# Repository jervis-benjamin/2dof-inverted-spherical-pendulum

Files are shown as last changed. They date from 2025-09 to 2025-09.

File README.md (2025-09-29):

# 2dof Inverted Spherical Pendulum

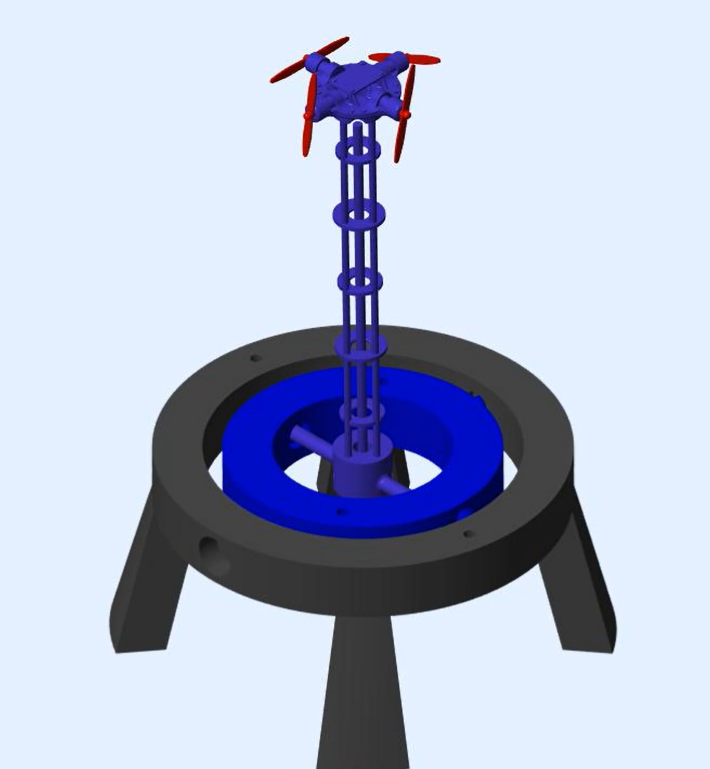
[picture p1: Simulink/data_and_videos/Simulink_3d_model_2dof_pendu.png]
model of the pendulum in Simulink


## Overview 🚀🌌
This project aims to keep an inverted pendulum (free to rotate about 2 axis) upright and balanced using orthogonally placed motors and propellors. Features include dedicated PID controllers, an extended Kalman filter for IMU sensor fusion, modeling system dynamics through Simulink, and hardware implementation through ESP32/Arduino components and CAD + 3D printing.

The goal of this project was to learn fundamentals of controls and design. Many of the components in this project are far from perfect, but they represent the time I’ve spent exploring a topic I care about.

### Here is the project broken up into its major sections, explained in further detail below:
- *CAD/Structure Design* 🧮📐
- *Simulation and Modeling* 🎯📊
- *Electronics, Controller Software, and Implementation* 🛠️🔌

### If you are interested in replicating or improving this project, here are the tools used:
*(These are just what I used, there are always better and more accessible options)*
- **CAD** -> Solidworks
- **3D printing** -> Cura, Ender 3
- **Simulation** -> Simulink
- **Controller Software** -> C++ (using an Arduino framework on Platform.io via VS Code)
- **Telemetry** -> VS Code Teleplot Extension

### Notable Materials/Items Used:
- ESP32 Dev Board
- Adafruit MPU-6050 6-DoF Accel and Gyro Sensor
- L298N DC Motor Driver Module (x2)
- LM2596 DC-DC Buck Power Converter Module
- 7x16 drone DC motors and propellers (x4)
- 18650 batteries (x2)
- 608 2RS Ball Bearings (x4)
- PLA filament rolls

## CAD/Structure Design 🧮📐
As mentioned before, all structural parts were custom made, 3D modeled and printed from PLA. This was to support the iterative process of building and testing prototypes, as well as enabling me to grow more on my knowledge of CAD and 3D printing. 

**The general structure can be mainly broken down into two sections:**
- The pendulum and supporting components
  - This includes the pendulum head (which houses the IMU and 4 motors), and the rod section (which extends the pendulum head down to the gimbal points).
- The bed
  - This includes the gimbal pieces which provide the 2 degrees of freedom, the stand which contains the pendulum, and the “electronics bay” which houses components such as the ESP32, battery, and motor control boards.
 
Within the CAD directory are both the .stl files and well as the Solidworks part + assembly files that were used to create this project.

## Simulation and Modeling 🎯📊
Euler-Langrage Equations of motion (overview of derivation linked in this pdf):

*Euler-Langrage Equations of motion for the pendulum*

To model the pendulum’s dynamics and simulate the control logic used, I learned how to use Simulink. There are many things to refine as this is the first model I have made in Simulink, but below is the general functionalities and structure of the program:

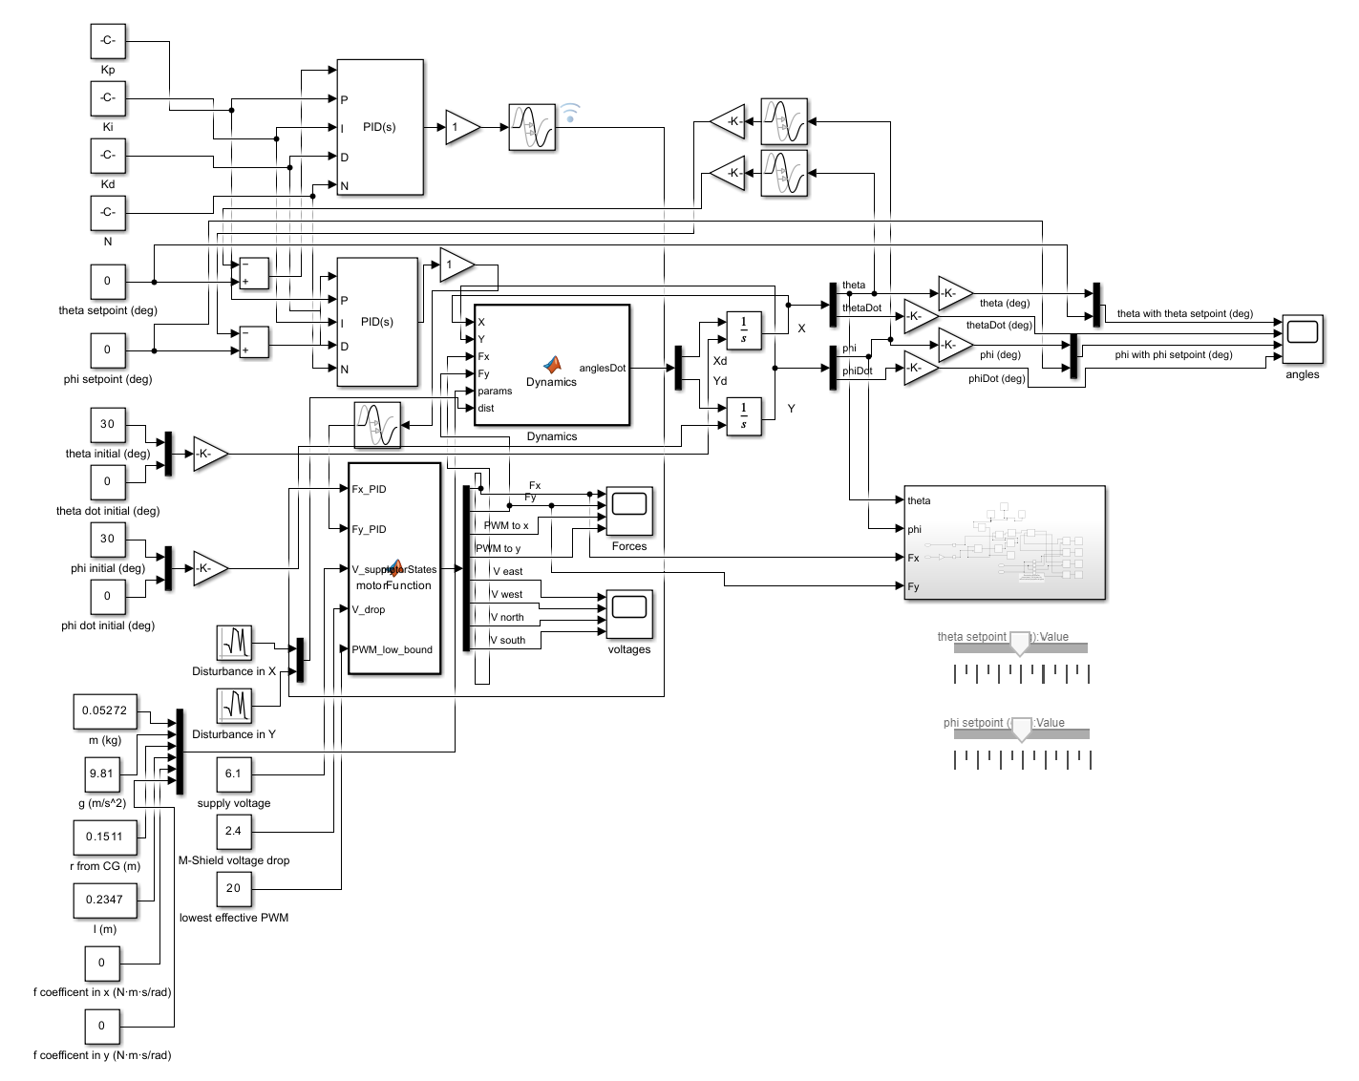
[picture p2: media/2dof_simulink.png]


- Implements PID control loops for each axis of control.
- Models dynamics via Euler-Lagrange equations of state as MATLAB functions.
- Mimics motor algorithms in controller code to show how a PID control output is being converted to a motor signal.
- Takes in parameters of real hardware
- Has the option to control the setpoint in real time to control the pendulum on user inputs.

**Simulation outputs**
- 3D visualization of pendulum performance (found in: Simulink/data_and_videos)
- Plots of relevant data such as angles, setpoints, forces, and motor commands over time
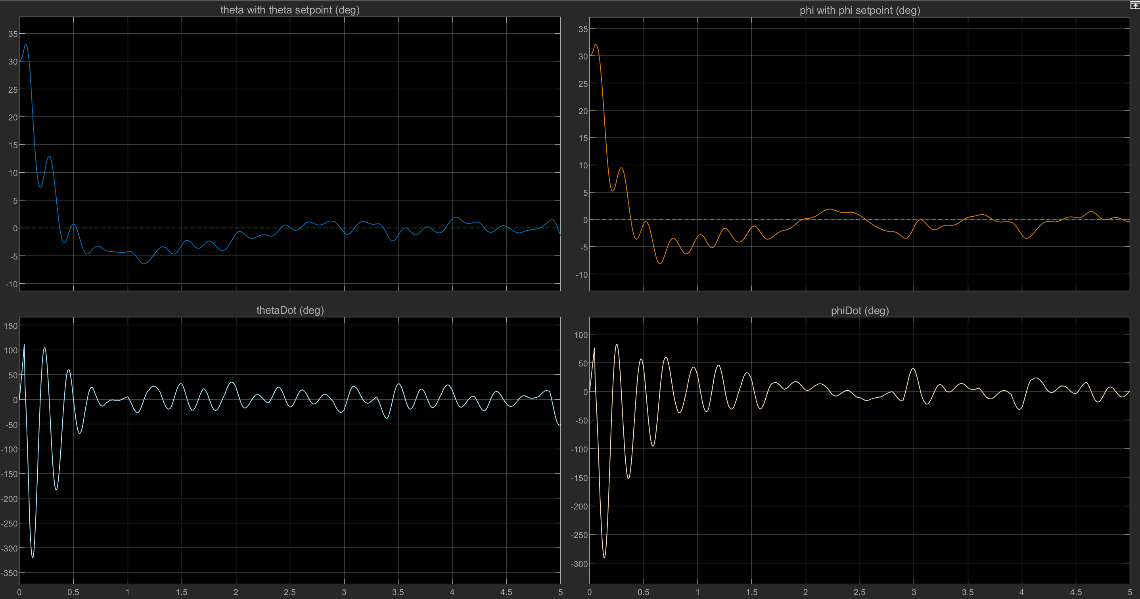
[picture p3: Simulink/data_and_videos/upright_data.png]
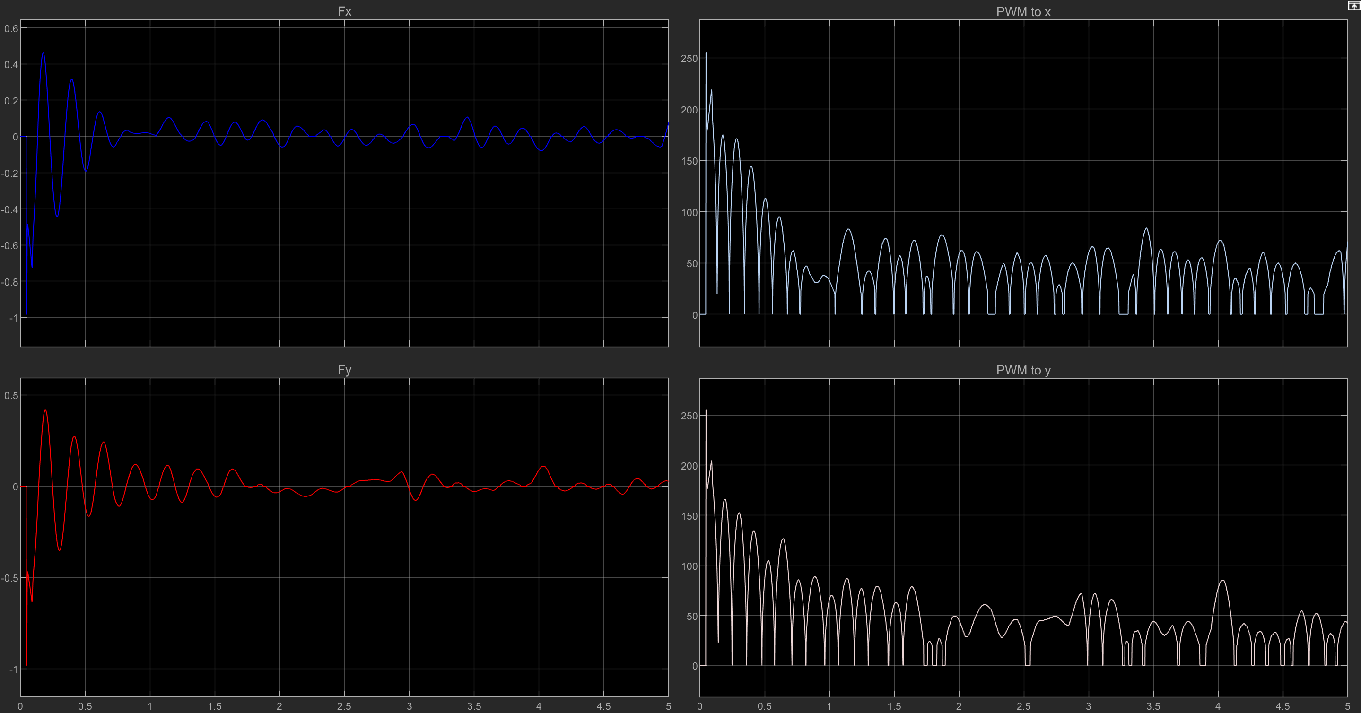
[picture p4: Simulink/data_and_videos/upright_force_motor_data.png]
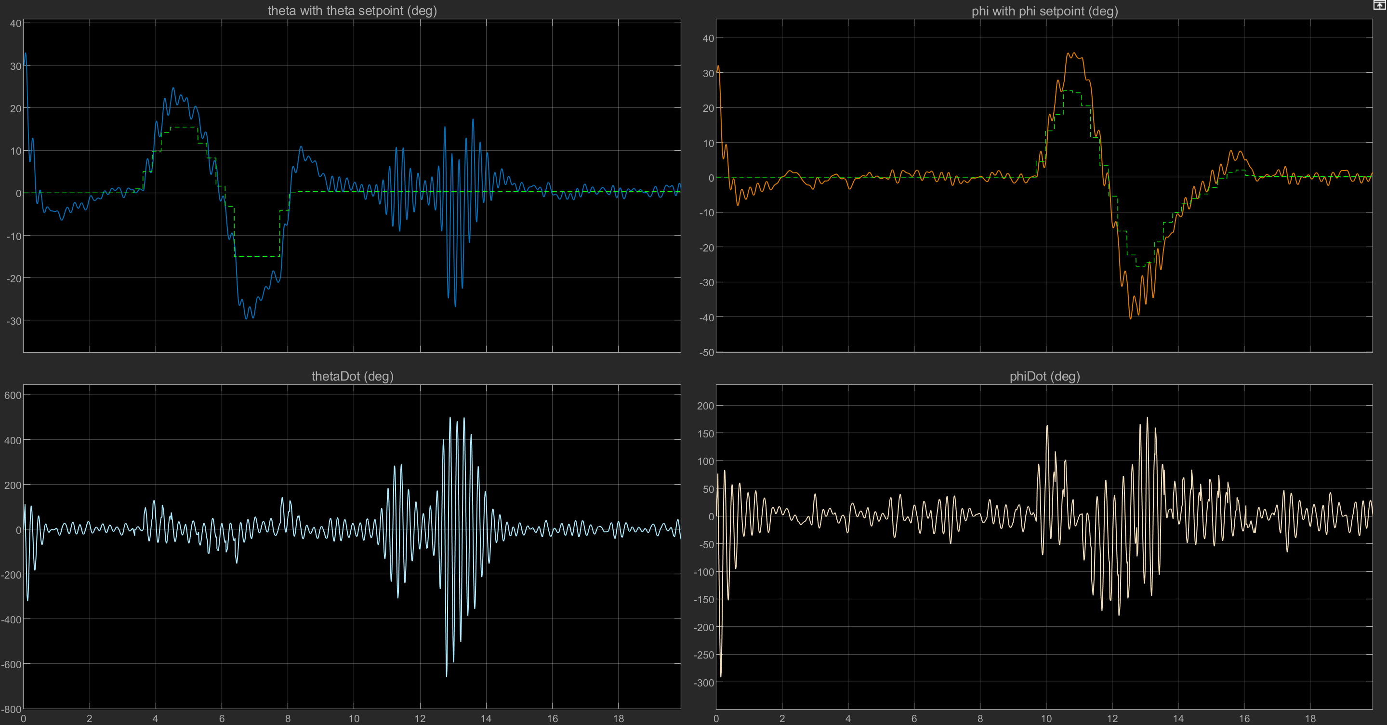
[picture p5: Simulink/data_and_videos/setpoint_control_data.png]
   

## Electronics, Controller Software, and Implementation 🛠️🔌
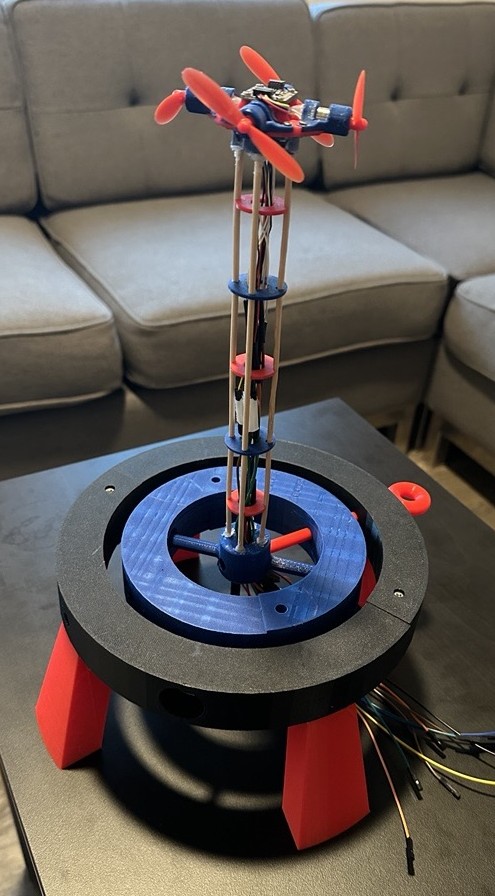
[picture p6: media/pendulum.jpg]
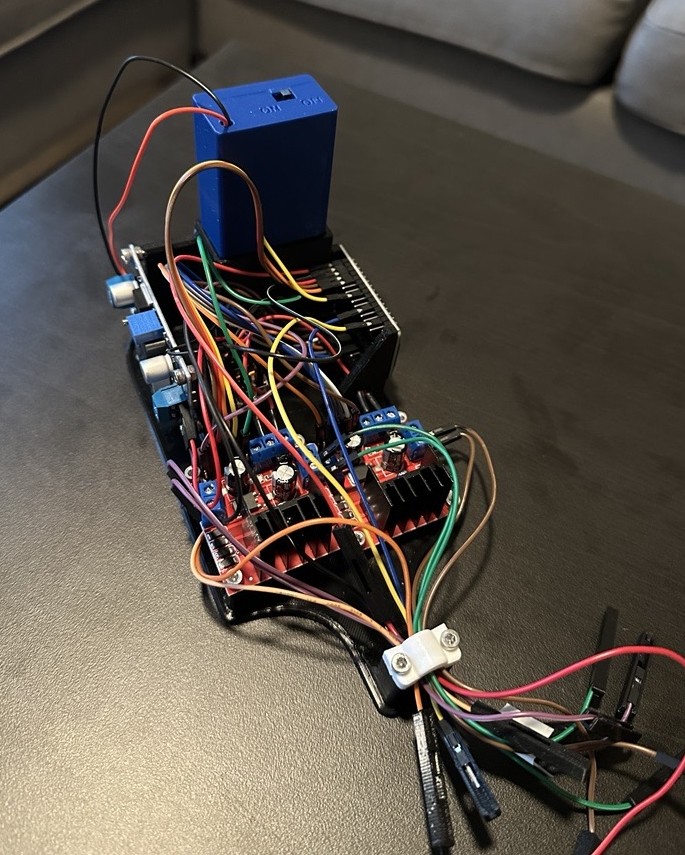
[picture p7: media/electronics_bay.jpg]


To interface with the hardware, I utilized a C++ controller program which ran on an ESP32 that linked communication between the IMU and motors. The step is the culmination of the CAD and design work to create a physical model.

**Features:**
- To gather usable angular position data from the IMU, an extended Kalman filter was utilized for accelerometer and gyroscope sensor fusion.
- Using the VS Code Teleplot extension, the controller code could display IMU and motor data as moving plots.
- The controller code supported user interaction via serial commands, allowing the user to change the pendulum setpoint at any time or run preprogrammed setpoint control programs.

Through testing and tunning, the pendulum was able to balance, though only within a small range. After referencing the simulation model, controller code, and the hardware performance, the biggest limitation to stability was the time taken for the propellors to spin fast enough to produce the required thrust. While the pendulum’s performance was not robust as originally planned, further steps can be taken for the future of this project (which are explained in the section below)

## Future Steps🛰️🔭
Overall, the large delay in the time that the propellors spin fast enough to provide the required torque prevents the level of stability that I am aiming for. Without much support, the pendulum fails to keep upright within a range larger than 5 degrees. In the future, I am planning to either account for this by implementing faster hardware or allowing the controller to better anticipate these delays. 

Additionally, I am hoping to increase the complexity of this project to allow me to dive deeper and apply more relevant concepts within controls. For example, I am considering adding another degree of freedom (rotation about the z axis), as well as integrating more complex controller logic such as LQR. Moreover, to better reflect the applicability of this project, I think it may be interesting to switch propulsion to cold gas thrusters to reflect a spacecraft's ability to use an RCS for attitude control.

To conclude, though the current set up is unable to bring the level of stability I was aiming for, I learned a lot through this process from software design to hardware implementation. I am determined to learn even more, and work on the ideas mentioned above to create a more sophisticated controls project.

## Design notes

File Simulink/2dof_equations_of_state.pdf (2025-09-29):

# 2dof Equations of State, Basic Overview

## References:

θ = tilt about the y axis, | ϕ = tilt about the x axis
rcm = length to the center of mass, | l = length of pendulum

L = T − U = KE − P E

d

dt
∂L
∂q˙
−

∂L
∂q = Q

Kinematics:

x = rcm sin θ cos ϕ, | y = rcm sin θ, | z = rcm cos θ cos ϕ

x˙ = rcm

˙θ cos θ cos ϕ − rcmϕ˙ sin θ sin ϕ

y˙ = rcmϕ˙ cos ϕ

z˙ = −rcm

˙θ sin θ cos ϕ − rcmϕ˙ cos θ sin ϕ

T =

1

2mv² =
1

2m( ˙x + ˙y + ˙z) = 1

2mr²

cm(ϕ˙² + ˙θ
2

cos² ϕ)

U = mgz = mgrcm cos θ cos ϕ

## Lagrangian

L = T − U =

1
2

mr²

cmϕ˙² +

1
2

mr²
cm

˙θ
2

cos² ϕ − mgrcm cos θ cos ϕ

—

1

## Equations of Motion

d

dt
∂L
∂ ˙θ
−

∂L
∂θ = τθ

d

dt
∂L
∂ϕ˙
−

∂L
∂ϕ = τϕ

Thus:

mr²
cm

¨θ cos² ϕ − mr²
cm

˙θϕ˙ sin(2ϕ) − mgrcm sin θ cos ϕ = τθ = Fxl

mrcmϕ¨ +

1
2

mr²
cm

˙θ
2
sin(2ϕ) − mgrcm cos θ sin ϕ = τϕ = Fyl

—

## State-Space Equations

Define states:
x1 = θ, | x2 = ˙θ, | y1 = ϕ, | y2 = ϕ˙

Dynamics:
x˙ 1 = x2 = ˙θ
x˙ 2 = ¨θ = | Fxl
mrcm cos² ϕ
| + | ˙θϕ˙ sin(2ϕ)
| | cos² ϕ | + g sin θ rcm cos ϕ

y˙1 = y2 = ϕ˙

y˙2 = ϕ¨ = | Fxl
mr²
| cm − ˙θ
| 2 | sin(2ϕ)
| | 2 + | g cos θ sin ϕ rcm

2

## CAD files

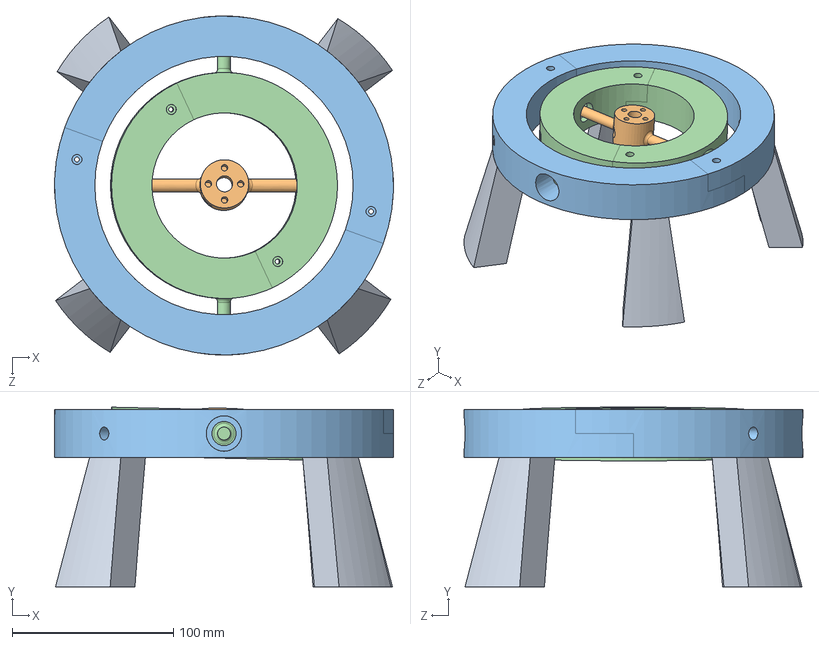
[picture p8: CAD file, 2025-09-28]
cad/solidworks/assemblies/2dof Bed.SLDASM
210.0 x 111.3 x 210.0 mm
inner_ring_2dof x 2
outer_ring_2dof x 2
core_2dof
leg_2dof x 4

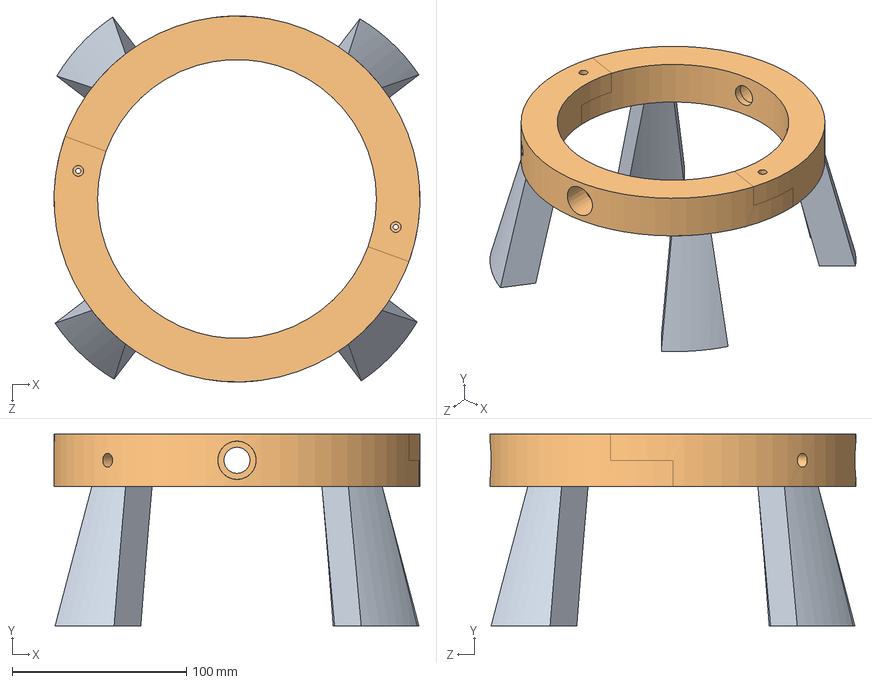
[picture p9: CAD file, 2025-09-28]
cad/solidworks/assemblies/Outer Ring Assembly.SLDASM
210.0 x 110.0 x 210.0 mm
outer_ring_2dof x 2
leg_2dof x 4

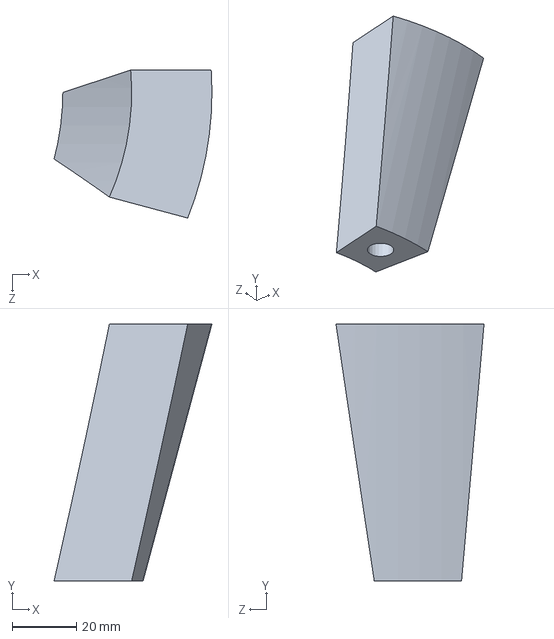
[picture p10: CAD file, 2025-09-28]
cad/solidworks/bed/leg_2dof.SLDPRT
49.2 x 80.0 x 46.1 mm

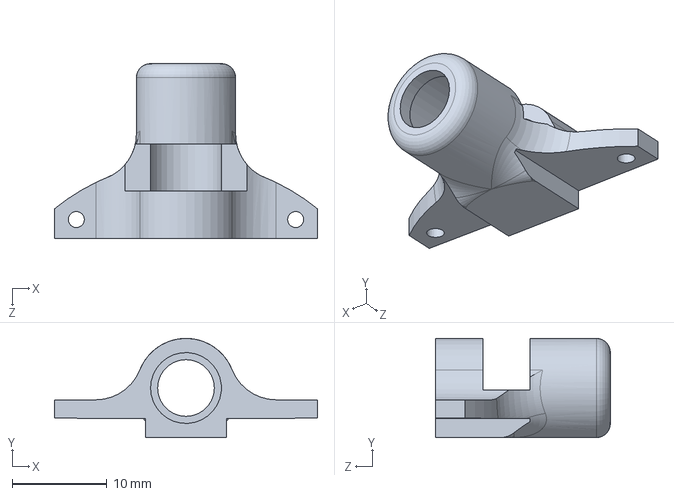
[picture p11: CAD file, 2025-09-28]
cad/solidworks/pendulum/pendu_V3_wing_2dof.SLDPRT
27.8 x 10.5 x 18.5 mm

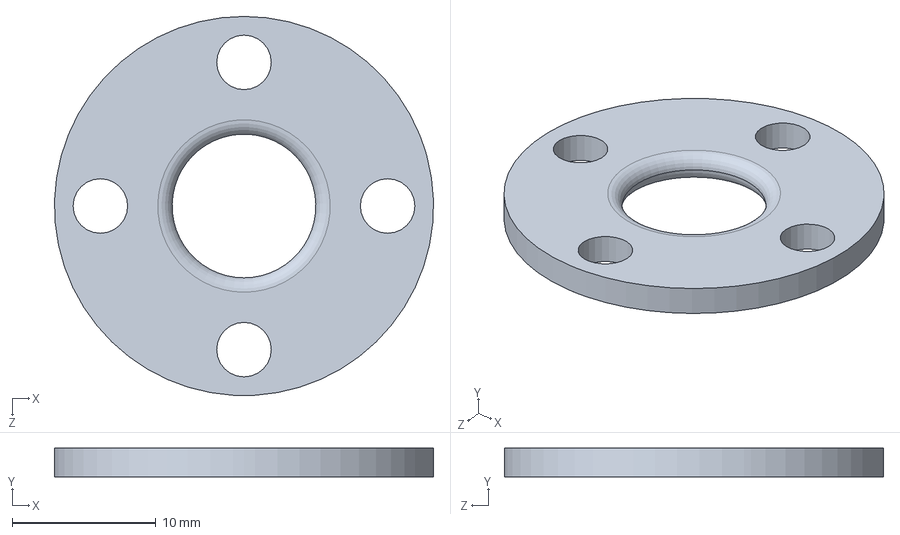
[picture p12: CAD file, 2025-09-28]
cad/solidworks/rod/a_support__2dof.SLDPRT
26.4 x 2.00 x 26.4 mm

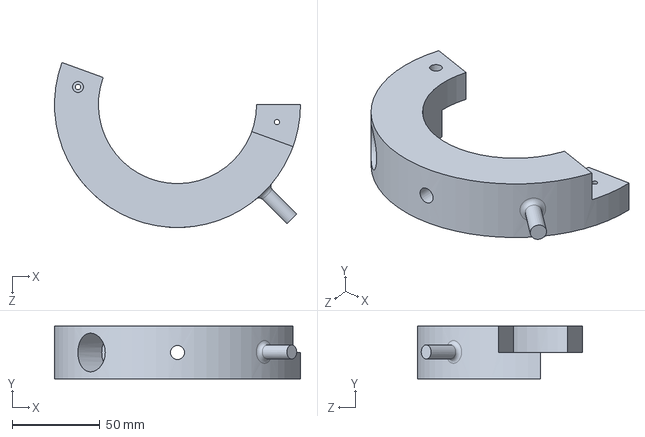
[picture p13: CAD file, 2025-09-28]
cad/solidworks/bed/inner_ring_2dof.SLDPRT
140.0 x 30.0 x 93.9 mm

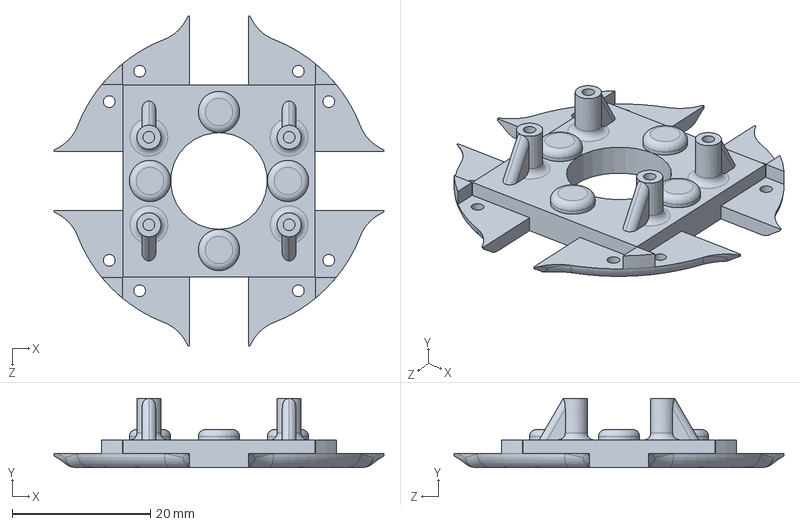
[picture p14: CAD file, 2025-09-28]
cad/solidworks/pendulum/pendu_V3_core_2dof.SLDPRT
47.8 x 10.0 x 47.8 mm

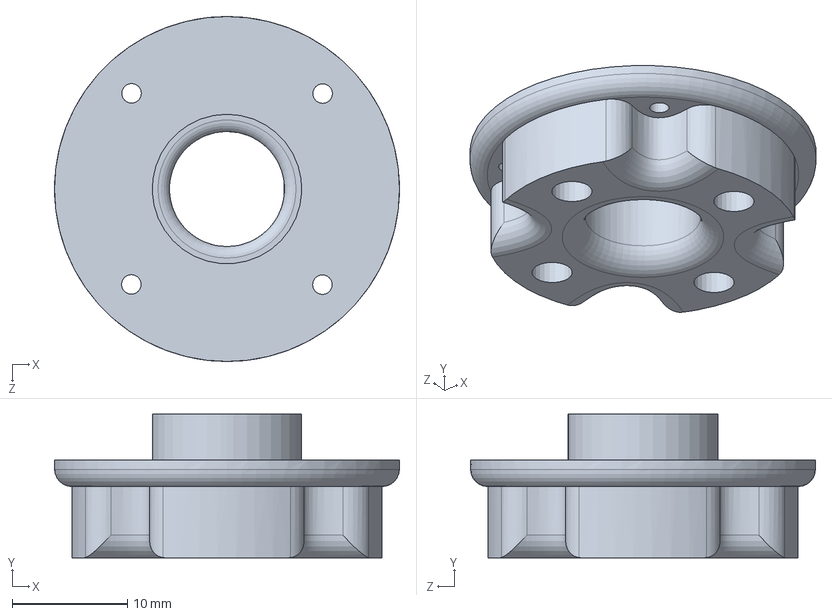
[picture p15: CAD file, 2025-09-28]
cad/solidworks/rod/rod_to_pendu_adapter_V3_2dof.SLDPRT
30.0 x 12.5 x 30.0 mm

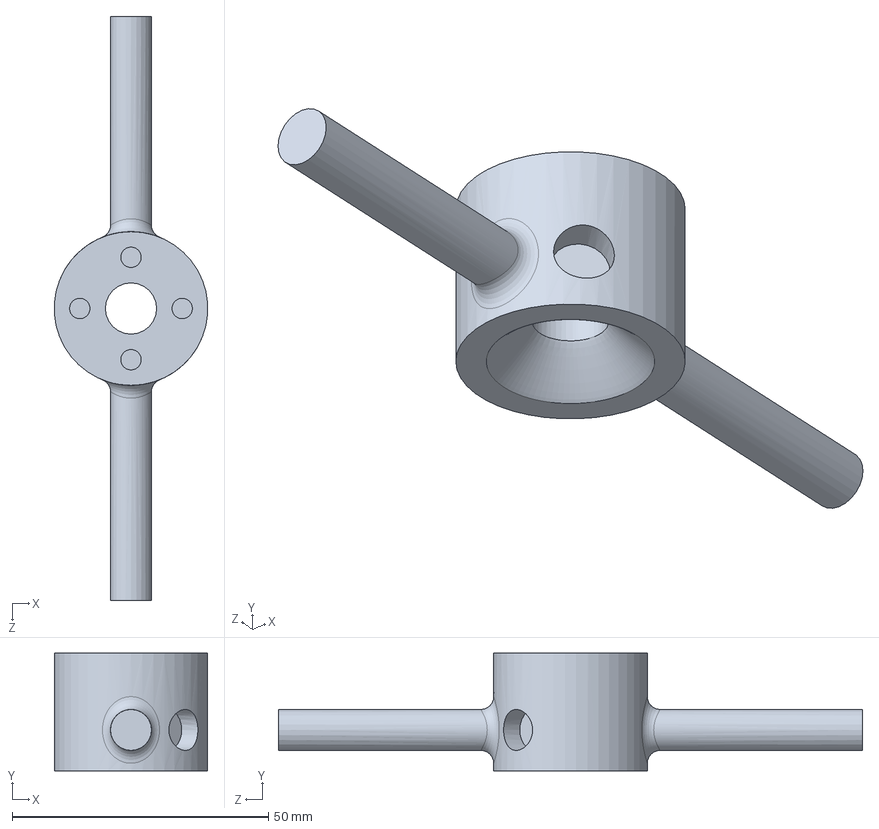
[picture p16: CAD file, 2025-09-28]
cad/solidworks/bed/core_2dof.SLDPRT
29.9 x 23.0 x 114.0 mm

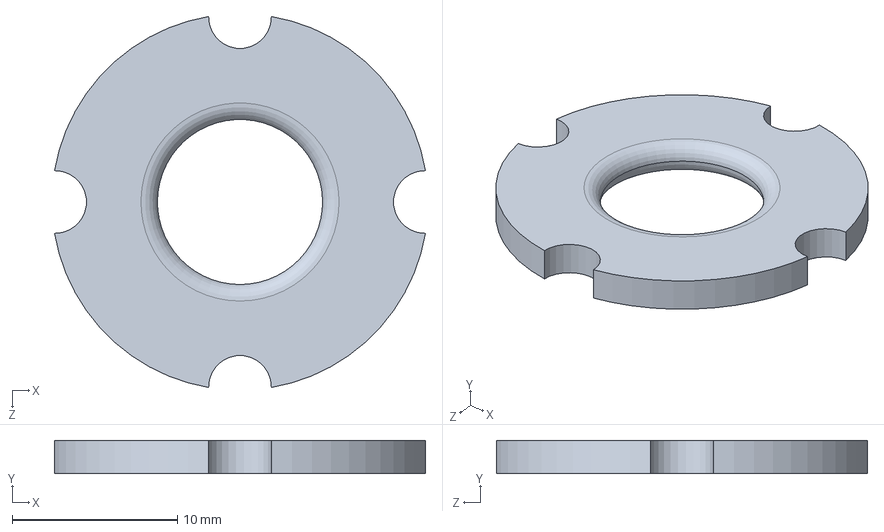
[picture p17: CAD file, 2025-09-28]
cad/solidworks/rod/b_support_V2_2dof.SLDPRT
22.5 x 2.00 x 22.5 mm

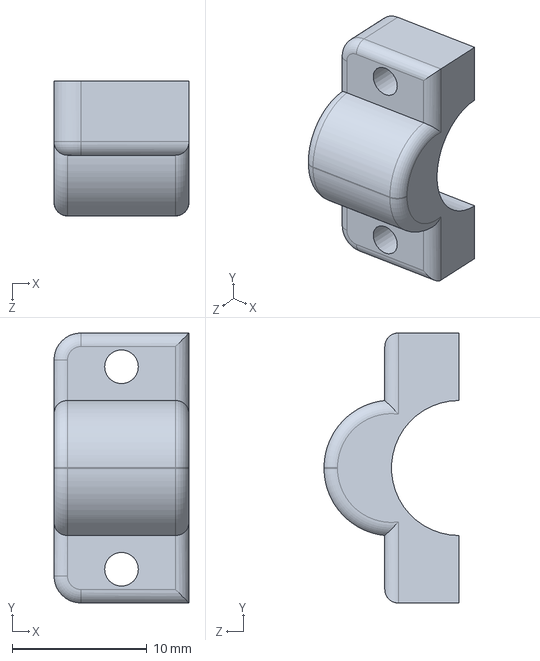
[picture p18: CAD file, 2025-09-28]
cad/solidworks/bed/electronics_bay_guide_2dof.SLDPRT
10.00 x 20.0 x 10.0 mm

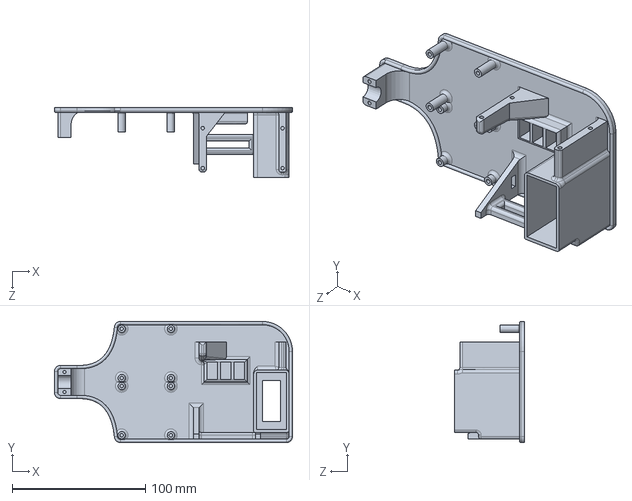
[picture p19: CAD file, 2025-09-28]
cad/solidworks/bed/electronics_bay_V2_2dof.SLDPRT
178.9 x 91.0 x 52.5 mm

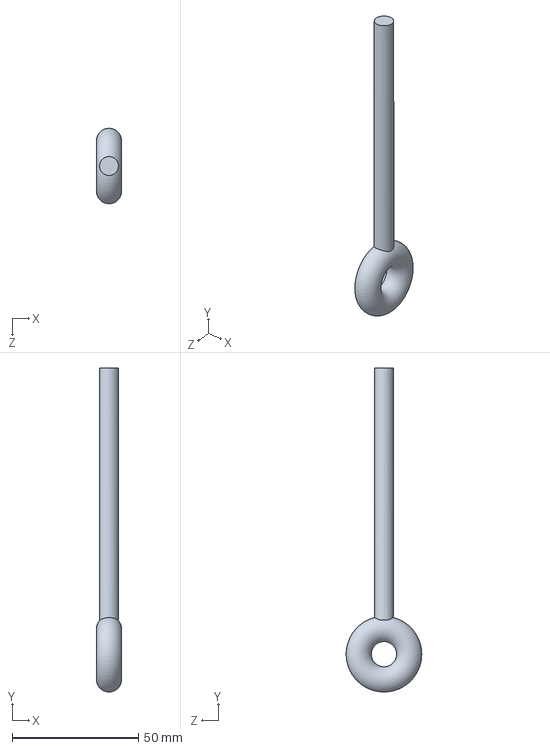
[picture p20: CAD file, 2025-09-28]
cad/solidworks/bed/pin_V3_2dof.SLDPRT
9.96 x 128.5 x 30.0 mm

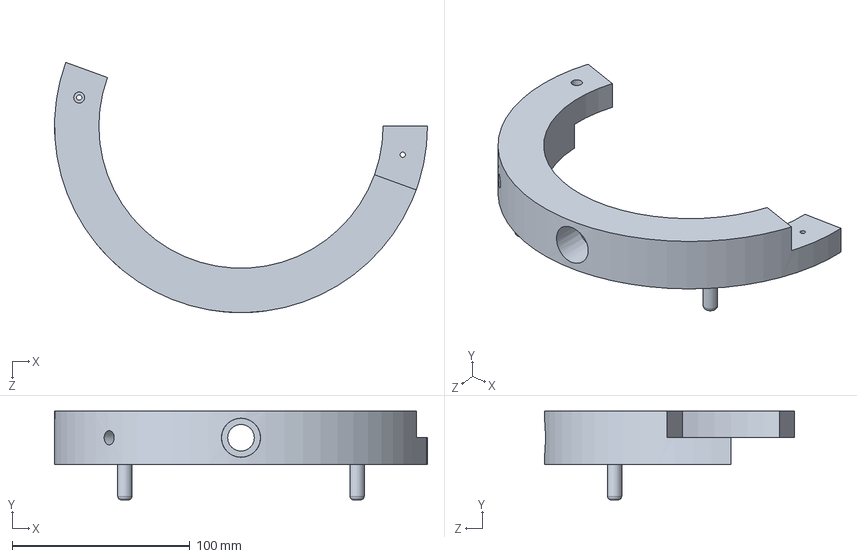
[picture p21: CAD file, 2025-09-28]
cad/solidworks/bed/outer_ring_2dof.SLDPRT
210.0 x 50.0 x 140.9 mm

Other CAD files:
cad/solidworks/assemblies/Inner Ring Assembly.SLDASM
cad/solidworks/assemblies/2dof Pendulum.SLDASM
cad/solidworks/assemblies/2dof Pendulum without props.SLDASM
cad/solidworks/bed/18650 battery holder cover.SLDPRT
cad/solidworks/bed/18650 battery holder.SLDPRT
cad/stl/bed/18650 battery holder cover.STL
cad/stl/bed/18650 battery holder.STL
cad/stl/bed/core_2dof.STL
cad/stl/bed/electronics_bay_V2_2dof.STL
cad/stl/bed/electronics_bay_guide_2dof.STL
cad/stl/bed/inner_ring_2dof.STL
cad/stl/bed/leg_2dof.STL
cad/stl/bed/outer_ring_2dof.STL
cad/stl/bed/pin_V3_2dof.STL
cad/stl/pendulum/pendu_V3_core_2dof.STL
cad/stl/pendulum/pendu_V3_wing_2dof.STL
cad/stl/rod/a_support__2dof.STL
cad/stl/rod/b_support_V2_2dof.STL
cad/stl/rod/rod_to_pendu_adapter_V3_2dof.STL

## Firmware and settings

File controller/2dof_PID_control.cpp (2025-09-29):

#include <Arduino.h>  
#include <Adafruit_MPU6050.h>
#include <Adafruit_Sensor.h>
#include <Wire.h>
#include <cmath>
#include <string>
#include <BasicLinearAlgebra.h>

using namespace BLA;
Adafruit_MPU6050 mpu;

/* motor variables and pins */
const int motorNorth = 13;
const int IN1_1 = 5;
const int IN2_1 = 4;

const int motorSouth = 12;
const int IN3_1 = 15;
const int IN4_1 = 2;

const int motorEast = 14;
const int IN1_2 = 27;
const int IN2_2 = 26;

const int motorWest = 25;
const int IN3_2 = 33;
const int IN4_2 = 32;

const int motor[2][2] = {{motorEast, motorWest}, {motorNorth, motorSouth}};
const int motorIN1[2][2] = {{IN1_2, IN3_2}, {IN1_1, IN3_1}};
const int motorIN2[2][2] = {{IN2_2, IN4_2}, {IN2_1, IN4_1}};

// offsets
double ACC_X_OFFSET = 0, ACC_Y_OFFSET = 0, ACC_Z_OFFSET = 0;
double GYR_X_OFFSET = 0, GYR_Y_OFFSET = 0, GYR_Z_OFFSET = 0;

// starting time
unsigned long t0 = 0;
unsigned long start_time = 0;

/* miscellaneous system parameters */
double thrust_limit = 0.56; // max magnetude of trust (in Newtons) from one motor set (two motors)
double supply_voltage = 4.8;
double voltage_drop = 2; // approximate voltage drop in the l298
int pwm_floor = 50, pwm_ceiling = 14000; // bounds for when to cut off motor to prevent buzzing or abort from saturation

/* PID variables for theta */
const double Kp_theta = 0.006, Ki_theta = 0.005036, Kd_theta = 0.01191, N_theta = 856.656;
double theta_setpoint = 0;
double theta_integral = 0;
double prev_theta_error = 0;
double filt_theta_derivative = 0;
double Theta;

/* PID variables for phi */
const double Kp_phi = 0.006, Ki_phi = 0.005036, Kd_phi = 0.01191, N_phi = 856.656;
double phi_setpoint = 0;
double phi_integral = 0;
double prev_phi_error = 0;
double filt_phi_derivative = 0;
double Phi;

/* total PID variables */
double Kp[2] = {Kp_theta, Kp_phi}, Ki[2] = {Ki_theta, Ki_phi}, Kd[2] = {Kd_theta, Kd_phi}, N[2] = {N_theta, N_phi};
double setpoint[2] = {theta_setpoint, phi_setpoint};
double integral[2] = {theta_integral, phi_integral};
double prev_error[2] = {prev_theta_error, prev_phi_error};
double filt_derivative[2] = {filt_theta_derivative, filt_phi_derivative};
double angle[2] = {Theta, Phi};
double PID_gain = 1;

/* PID controller function */
double applyPID(double angle, int angle_mode, double dt){

  if (dt > 0.01) dt = 0.01; // clamp at 20 ms
  if (dt < 0.001) dt = 0.001; // clamp to avoid zero

  double error = setpoint[angle_mode] - angle; // computing error

  /* computing integral */
  double integral_max = 0, integral_min = 0;
  if (Ki[angle_mode] != 0) {
      integral_max = thrust_limit / fabs(Ki[angle_mode]);
      integral_min = -thrust_limit / fabs(Ki[angle_mode]);
  }

  integral[angle_mode] += (error * dt);

  // integral anti-windup
  if(integral[angle_mode] > integral_max){ 
    integral[angle_mode] = integral_max;
  }else if (integral[angle_mode] < integral_min){
    integral[angle_mode] = integral_min;
  }

  /* computing derivative */
  double derivative = (error - prev_error[angle_mode]) / dt;
  double filtered_derivative = (N[angle_mode] * filt_derivative[angle_mode] + derivative) / (N[angle_mode] + 1); // applying a low pass filter on the derivative term
  filt_derivative[angle_mode] = filtered_derivative; // updating previous error
  prev_error[angle_mode] = error; // updating previous error

  // determine PID output
  double force = PID_gain * (Kp[angle_mode] * error) + (Ki[angle_mode] * integral[angle_mode]) + (Kd[angle_mode] * filtered_derivative);

  return force;
}

/* motor control algorthim: takes in PID output and actuates motors*/
double applyCorrectiveTrust(double force, int angle_mode){

  // calculating pwm motor signal to determine motor speed
  int motorSpeed = round(sqrt(fabs(force)/0.0359 ) * (255/(supply_voltage-voltage_drop))); 

  if(motorSpeed > pwm_ceiling){
    motorSpeed = 0; // cutting off thrust when system is saturated
  }else if(motorSpeed > 255){
    motorSpeed = 255; // allowing max thrust when the system is only slightly saturated
  }else if(motorSpeed < pwm_floor){
    motorSpeed = pwm_floor; // turning motor off to prevent buzzing from low pwm
  }

  if((motorSpeed == 0) || (fabs(angle[angle_mode]) > 45)){
    digitalWrite(motorIN1[angle_mode][0], LOW);
    digitalWrite(motorIN2[angle_mode][0], LOW);
    analogWrite(motor[angle_mode][0], 0);
    digitalWrite(motorIN1[angle_mode][1], LOW);
    digitalWrite(motorIN2[angle_mode][1], LOW);
    analogWrite(motor[angle_mode][1], 0);
  }else if(force > 0){
    digitalWrite(motorIN1[angle_mode][0], HIGH);
    digitalWrite(motorIN2[angle_mode][0], LOW);
    analogWrite(motor[angle_mode][0], motorSpeed);
    digitalWrite(motorIN1[angle_mode][1], LOW);
    digitalWrite(motorIN2[angle_mode][1], HIGH);
    analogWrite(motor[angle_mode][1], motorSpeed);
  }else if(force < 0){
    digitalWrite(motorIN1[angle_mode][0], LOW);
    digitalWrite(motorIN2[angle_mode][0], HIGH);
    analogWrite(motor[angle_mode][0], motorSpeed);
    digitalWrite(motorIN1[angle_mode][1], HIGH);
    digitalWrite(motorIN2[angle_mode][1], LOW);
    analogWrite(motor[angle_mode][1], motorSpeed);
  }
  
  return motorSpeed;
}

/* Extended Kalman Filter variables */
Matrix<6,1,double> x_hat = {0, 0, 0, 0, 0, 0}; // state vector x_hat = {theta prediction, phi prediction, theta velocity, phi velocity, gyro bias in x dir, gyro bias in y dir}

Matrix<6,6,double> P = {0.1,   0,     0,     0,     0,     0, // state covariance matrix
                        0,     0.1,   0,     0,     0,     0,
                        0,     0,     0.1,   0,     0,     0,
                        0,     0,     0,     0.1,   0,     0,
                        0,     0,     0,     0,     0.001, 0,
                        0,     0,     0,     0,     0,     0.001};

Matrix<6,6,double> Q = {35,      0,       0,       0,       0,       0, // process noise covariance matrix
                        0,       5,       0,       0,       0,       0,
                        0,       0,       27,      0,       0,       0, 
                        0,       0,       0,       12,      0,       0,
                        0,       0,       0,       0,       0.001,   0,
                        0,       0,       0,       0,       0,       0.002};

Matrix<2,2,double> R = {2000, 0, // measurement noise covariance matrix
                        0, 1000};
                        
Matrix<2,6,double> H = {1, 0, 0, 0, 0, 0, // measurement Jacobian matrix
                        0, 1, 0, 0, 0, 0};

Matrix<6,6,double> F; // state transition Jacobian matrix
Matrix<2,2,double> S; // innovation covariance matrix
Matrix<6,2,double> K; // Kalman gain

Matrix<6,6,double> I = {1,0,0,0,0,0, // identity matrix
                        0,1,0,0,0,0,
                        0,0,1,0,0,0,
                        0,0,0,1,0,0,
                        0,0,0,0,1,0,
                        0,0,0,0,0,1};


/* applies an Extended Kalman Filter */
void KalmanFilter(double gyr_x, double gyr_y, double acc_x, double acc_y, double acc_z, double dt){ 
  
  if (dt > 0.01) dt = 0.01; // clamp at 20 ms
  if (dt < 0.001) dt = 0.001; // clamp to avoid zero

  /* ------------PREDICT------------ */

  // updating state vector
  x_hat(0,0) = x_hat(0,0) + (gyr_y - x_hat(5,0)) * dt; // updating theta prediction
  x_hat(1,0) = x_hat(1,0) + (gyr_x - x_hat(4,0)) * dt; // updating phi prediction
  x_hat(2,0) = gyr_y - x_hat(5,0); // updating theta angular velocity
  x_hat(3,0) = gyr_x - x_hat(4,0); // updating phi angular velocity

  F = {1,  0,  dt, 0,  0,  0, // updating state transition Jacobian matrix
       0,  1,  0,  dt, 0,  0,
       0,  0,  1,  0, -dt, 0,
       0,  0,  0,  1,  0, -dt,
       0,  0,  0,  0,  1,  0,
       0,  0,  0,  0,  0,  1};

  P = F * P * ~F + Q; // covariance prediction


  /* ------------UPDATE------------ */

  S = H * P * ~H + R; // updating the total uncertainty
  S(0,0) += 1e-6; // regularize S Before Inversion
  S(1,1) += 1e-6;
  K = P * ~H * Inverse(S); // computing Kalman gain

  double theta_meas = atan2(acc_x, acc_z); // theta measurment from accelerometer
  double phi_meas = atan2(acc_y, acc_z); // phi measurment from accelerometer
  Matrix<2,1,double> z = {theta_meas, phi_meas}; // measurement vector
  
  x_hat = x_hat + K * (z - (H * x_hat)); // updating state estimates with measurements
  P = (I - K * H) * P; // updating the state covariance matrix
  P = 0.5 * (P + ~P); // forcing symmetry since computational truncation or rounding can prevent symmetry

   // for error checking
  for (int i = 0; i < 6; i++) {
    if (isnan(x_hat(i,0)) || isinf(x_hat(i,0))) {
      Serial.println("Invalid element in x_hat!");
      x_hat(i,0) = 0;
    }
  }2
  for (int i = 0; i < 6; i++) {
    if (isnan(P(i,i)) || isinf(P(i,i))) {
      Serial.println("Invalid element in P!");
      P(i,i) = 0;
    }
  }
}



/*---------------------------------------angle setpoint commands here---------------------------------------*/
bool run_pitch_sweep = false;
unsigned long pitch_sweep_start_t, pitch_sweep_t_elapsed;
void pitchSweep(double pitch_range){ // sweeping pitch angle without ramping
   
  unsigned long elapsed_time = millis() - pitch_sweep_start_t;
  if(elapsed_time < 500){
    theta_setpoint = 0;
  }else if(elapsed_time < 4500){
    theta_setpoint = pitch_range;
  }else if(elapsed_time < 8500){
    theta_setpoint = 0;
  }else if(elapsed_time < 12500){
    theta_setpoint = -pitch_range;
  }else if(elapsed_time < 15500){
    theta_setpoint = 0;
  }else{
    run_pitch_sweep = false;
  }
}

bool run_ramp_pitch_sweep = false;
unsigned long ramp_pitch_sweep_start_t, ramp_pitch_sweep_t_elapsed;
void rampPitchSweep(double pitch_range){ // half a second at 0 to reset, 1 second to ramp to range, 3 seconds to hold, one second to ramp to 0, 1 second to hold (then repeat for negative side), end at 0 and hold for 2 seconds

  pitch_range = fabs(pitch_range); // making sure the range will always be a magnetude
  unsigned long elapsed_time = millis() - ramp_pitch_sweep_start_t;
  if(elapsed_time < 500){
    theta_setpoint = 0;
  }else if(elapsed_time < 1500){
    theta_setpoint += (pitch_range/100);
  }else if(elapsed_time < 4500){
    theta_setpoint = pitch_range;
  }else if(elapsed_time < 5500){
    theta_setpoint -= (pitch_range/100);
  }else if(elapsed_time < 6500){
    theta_setpoint = 0;
  }else if(elapsed_time < 7500){
    theta_setpoint -= (pitch_range/100);
  }else if(elapsed_time < 10500){
    theta_setpoint = -pitch_range;
  }else if(elapsed_time < 11500){
    theta_setpoint += (pitch_range/100);
  }else if(elapsed_time < 13500){
    theta_setpoint = 0;
  }else{
    run_ramp_pitch_sweep = false;
  }
}

/*---------------------------------------------------------------------------------------------------*/



void setup() {
  Serial.begin(115200);
  Serial.setTimeout(0); // changing delay to 0s instead of the default 1s for serial commands 

  for(int i = 0; i < 2; i++){
    for(int j = 0; j < 2; j++){
      pinMode(motor[i][j], OUTPUT);
      pinMode(motorIN1[i][j], OUTPUT);
      pinMode(motorIN2[i][j], OUTPUT);
    }
  }

  while (!Serial){ // waiting until serial console opens
    delay(10);
  }

  if (!mpu.begin()) {
    Serial.println("Failed to find MPU6050 chip");
    while (1){ 
      delay(10); 
    }
  }

  delay(2000); // delay to prevent serial prompts from being cut

  mpu.setAccelerometerRange(MPU6050_RANGE_8_G);
  mpu.setGyroRange(MPU6050_RANGE_500_DEG);
  mpu.setFilterBandwidth(MPU6050_BAND_21_HZ);

  /*IMU CALIBRATION*/
  Serial.println("IMPORTANT: Calibration sequence assumes custom IMU axis orientation");
  Serial.println("Verify that intended IMU axis and code orientations are similar!");
  Serial.println("===================================================================\n");
  Serial.println("2DOF_PID_CONTROL.cpp");
  Serial.println("Starting IMU calibration in 5 seconds");
  Serial.println("Ensure IMU is stable and upright. Do not move!");
  for(int i = 1; i <= 5; i++){
    Serial.print(i);
    Serial.println("...  ");
    delay(1000);
  }

  Serial.println("\nRecording IMU offsets...");
  sensors_event_t a, g, temp;

  Serial.print("[");
  int offset_sample_count = 2000;
  for(int i = 1; i <= offset_sample_count; i++){
    mpu.getEvent(&a, &g, &temp);
    ACC_X_OFFSET += a.acceleration.x;
    ACC_Y_OFFSET += a.acceleration.y;
    ACC_Z_OFFSET += a.acceleration.z;
    GYR_X_OFFSET += g.gyro.x;
    GYR_Y_OFFSET += g.gyro.y;
    GYR_Z_OFFSET += g.gyro.z;
    
    if (i%(offset_sample_count/5) == 0){
      Serial.print("==");
    }
  }
  
  ACC_X_OFFSET = ACC_X_OFFSET / offset_sample_count;
  ACC_Y_OFFSET = ACC_Y_OFFSET / offset_sample_count;
  ACC_Z_OFFSET = ACC_Z_OFFSET / offset_sample_count - 9.81;
  GYR_X_OFFSET = GYR_X_OFFSET / offset_sample_count;
  GYR_Y_OFFSET = GYR_Y_OFFSET / offset_sample_count;
  GYR_Z_OFFSET = GYR_Z_OFFSET / offset_sample_count;

  Serial.println("] Done!");

  /* Print out offsets */
  Serial.println("------------------------------------------------");
  Serial.print("Acceleration offsets X: ");
  Serial.print(ACC_X_OFFSET);
  Serial.print(", Y: ");
  Serial.print(ACC_Y_OFFSET);
  Serial.print(", Z: ");
  Serial.print(ACC_Z_OFFSET);
  Serial.println(" m/s^2");

  Serial.print("Rotation offsets X: ");
  Serial.print(GYR_X_OFFSET);
  Serial.print(", Y: ");
  Serial.print(GYR_Y_OFFSET);
  Serial.print(", Z: ");
  Serial.print(GYR_Z_OFFSET);
  Serial.println(" rad/s");
  Serial.println("------------------------------------------------");

  
  Serial.println("\n\n-- Beginning control loop in 5 seconds --");
  Serial.println("\nCommands: ");
  Serial.println("test - confirms serial messages and returns dt");
  Serial.println("t# - changes theta setpoint with # being a number between -45 to 45");
  Serial.println("p# - changes phi setpoint with # being a number between -45 to 45");
  Serial.println("a - abort");
  Serial.println("(Units -> accel: m/s^2, gyro: rad/s, angles: deg)");
  
  delay(5000); // delay to prepare for data collection

  Serial.println("\n------------------------------------------------\n\n");
  t0 = micros();
  start_time = micros();
}

void loop() {

  unsigned long t = micros();
  double dt = (t - t0) / 1e6; // since micros() returns in microseconds, we need to convert to seconds
  t0 = t;
  unsigned long elapsed_time = micros() - start_time;

  sensors_event_t a, g, temp;
  mpu.getEvent(&a, &g, &temp); 

  /* Applying offsets */
  double acc_x = -1 * (a.acceleration.x - ACC_X_OFFSET);
  double acc_y = -1 * (a.acceleration.y - ACC_Y_OFFSET);
  double acc_z = a.acceleration.z - ACC_Z_OFFSET;
  double gyr_x = -1 * (g.gyro.x - GYR_X_OFFSET);
  double gyr_y = -1 * (g.gyro.y - GYR_Y_OFFSET);
  double gyr_z = g.gyro.z - GYR_Z_OFFSET;

  /* computing angle values from the Kalman filter */
  KalmanFilter(gyr_x, gyr_y, acc_x, acc_y, acc_z, dt);
  double Theta = x_hat(0,0) * (180/M_PI);
  double Phi = x_hat(1,0) * (180/M_PI);

  double correct_force_x = applyPID(Theta, 0, dt);
  double correct_force_y = applyPID(Phi, 1, dt);

  int motor_speed_x = applyCorrectiveTrust(correct_force_x, 0);
  int motor_speed_y = applyCorrectiveTrust(correct_force_y, 1);

  if(Serial.available()){ // handles serial prompts for user commands
    String cmd = Serial.readStringUntil('\n');
    char cmd_type = cmd[0];

    if(cmd_type == 'a'){ // abort
        
      for(int i = 0; i < 2; i++){
        for(int j = 0; j < 2; j++){
          digitalWrite(motorIN1[i][j], LOW);
          digitalWrite(motorIN2[i][j], LOW);
          analogWrite(motor[i][j], 0);
        }
      }
        
      Serial.println("Program stopped");
      while(1){
        delay(10);
      }
    }

    if(cmd == "pitchsweep"){
      run_pitch_sweep = true;
      Serial.println("Running pitch sweep");
      pitch_sweep_start_t = millis();
    }else if(cmd == "pitchsweepramp"){
      run_ramp_pitch_sweep = true;
      Serial.println("Running pitch sweep (ramp ver.)");
      ramp_pitch_sweep_start_t = millis();
    }

    if(cmd.length() > 1){
      String cmd_val = cmd.substring(1);
      cmd_val.trim();

      const char *cstr = cmd_val.c_str(); // needed to verify if cmd_val can be succesfully converted
      char *endptr;
      double inputNum = strtof(cstr, &endptr);

      if((endptr != cstr) && (*endptr == '\0') && (inputNum >= -90) && (inputNum <= 90)){
        if(cmd_type == 't'){
          theta_setpoint = inputNum;
          Serial.print("New theta setpoint: ");
          Serial.println(theta_setpoint);
        }else if (cmd_type == 'p'){
          phi_setpoint = inputNum;
          Serial.print("New phi setpoint: ");
          Serial.println(phi_setpoint);
        }
      }
    }
  }  

  if(run_pitch_sweep){
    pitchSweep(10);
  }else if(run_ramp_pitch_sweep){
    rampPitchSweep(10);
  }

  // formatting data to be interpreted by Teleplot extension
  Serial.print(">Theta:"); Serial.println(Theta);
  Serial.print(">Phi:"); Serial.println(Phi);
  Serial.print(">theta_setpoint:"); Serial.println(theta_setpoint);
  Serial.print(">phi_setpoint:"); Serial.println(phi_setpoint);

  Serial.print(">motor_speed_x:"); Serial.println(motor_speed_x);
  Serial.print(">motor_speed_y:"); Serial.println(motor_speed_y);

  Serial.print(">time:"); Serial.println(elapsed_time);
  Serial.print(">dt:"); Serial.println(dt);

}

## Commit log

2025-09-28 Create cad folder
2025-09-28 Store stl files
2025-09-28 Store assembly files
2025-09-28 Store bed components
2025-09-28 Store rod components
2025-09-29 Update CAD folder
2025-09-29 Update assemblies folder
2025-09-29 Update bed folder
2025-09-29 Update rod folder
2025-09-29 Update stl folder
